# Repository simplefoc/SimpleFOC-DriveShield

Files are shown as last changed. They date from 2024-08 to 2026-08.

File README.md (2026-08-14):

# *Simple**FOC*** ***Drive**Shield* *v1.8*

 
 

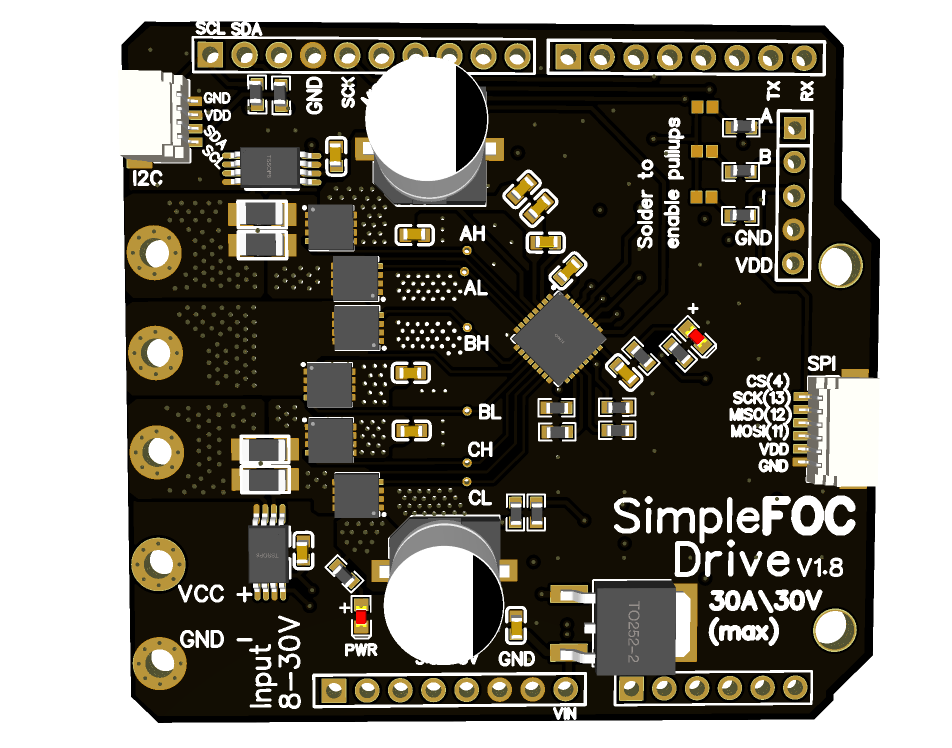
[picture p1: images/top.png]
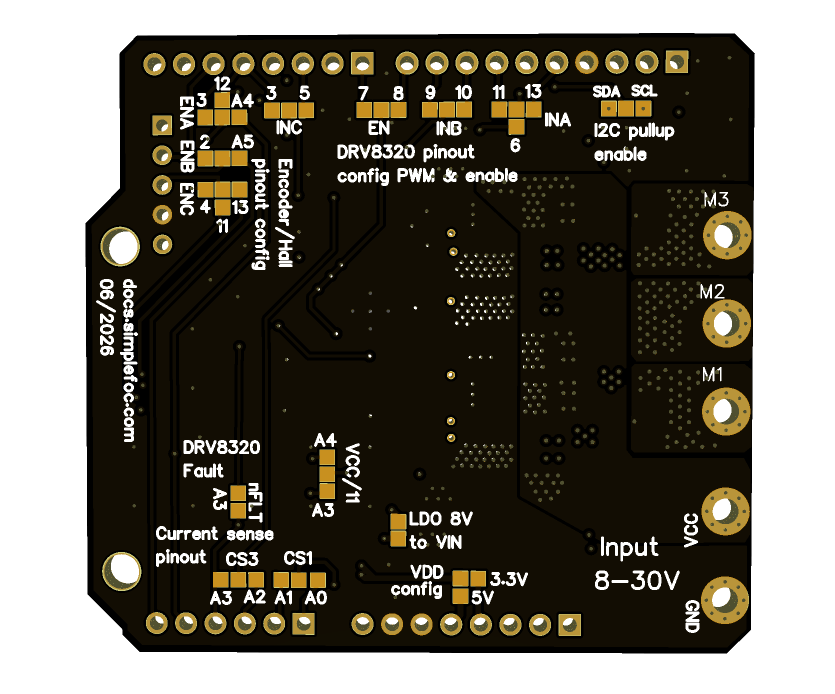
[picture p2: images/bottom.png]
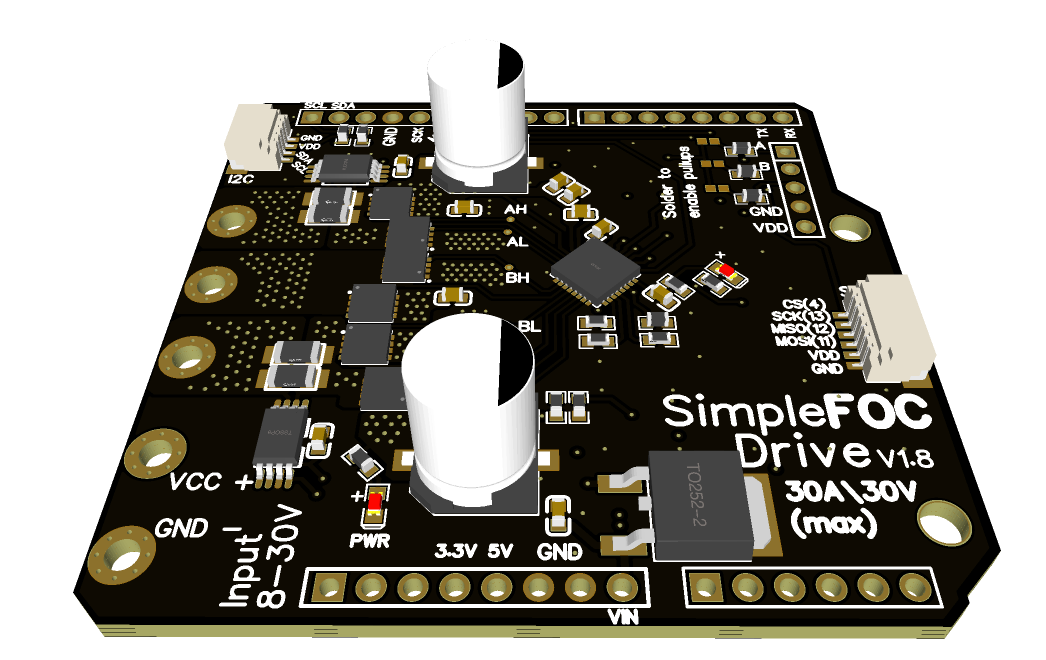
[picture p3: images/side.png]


This is an open-source low-cost BLDC driver boards in the form of a Arduino shield. It is a part of the *Simple**FOC*** project. The board is the big brother of the *Simple**FOC**Shield* and is designed to drive motors with higher current requirements, up to 40Amps. The board is created with the same philosophy as the *Simple**FOC**Shield* - to be simple to use, low-cost, and open-source and fully compatible with the *Simple**FOC***library. 

Additionally the aim of the board is to serve as a template project for the community to build their own motor drivers. 
- The board is relatively simple and can be easily modified to fit different requirements.
- The board is designed in EasyEDA and all the fabrication files are available for download

### Components
- **DRV8320H** gate driver - [datahseet](https://www.ti.com/lit/ds/symlink/drv8320.pdf?ts=178671431434)
   - Hardware configuration 
   - 3PWM 
   - Protections: undervoltage lockout, charge pump fault, MOSFET overcurrent, MOSFET short circuit, gate driver fault and overtemperature
- **BSZ0904NSI** mosfets
   - Standard 3mm x 3mm footprint (can be easily exchanged)
   - Max current 75A 
   - Max voltage 30V
- **INA240A1**: - [datasheet](https://www.ti.com/lit/ds/symlink/ina240.pdf?ts=1786684614540)
   - Inline current sensor
   - Gain 20V/V
   - Shunt resistor: 2mΩ (parallel of 4mΩ)
   - 40A measurement range bidirectional (at 3.3V)
- **LM7808**:
   - 8V LDO voltage regulator to VIN 

### Features
- **Boards absolute max ratings** 
   - Max current: 20A continuous (peak 30A - measured) 
   - Max input voltage: 30V
- **Stackable**: running 2 motors in the same time
- **Encoder/Hall sensors interface**: Integrated 3.3kΩ pullups (configurable)
- **I2C interface**: Integrated 4.7kΩ pullups (configurable)
- **Configurable pinout**: Hardware configuration - soldering connections
- **stemma QT connector**: for easy connection of sensors and peripherals
- **JST SPI connector**: for easy connection of SPI devices (only one SPI device can be connected at a time)
- **Arduino headers**: Arduino UNO, Arduino MEGA, STM32 Nucleo boards...
- **Open Source**: 
   - Fully designed in **EasyEDA**: [EasyEDA project](https://oshwlab.com/the.skuric/SimpleFOC-Drive)
   - Fully available fabrication files - [how to make it yourself](https://docs.simplefoc.com/arduino_simplefoc_shield_fabrication)
- **Low-cost**: Estimated price of 25-40€ - *Will be available through **Makerfabs** soon*

## Shield version comparison

Feature | <span class="simple">Simple<span class="foc">FOC</span>Shield</span> v1.x | <span class="simple">Simple<span class="foc">FOC</span>Shield</span> v2.x | <span class="simple">Simple<span class="foc">FOC</span>Shield</span> v3.x | <span class="simple">Simple<span class="foc">FOC</span> <b>Drive</b>Shield</span> v1.x
|-|-|-|-|-|
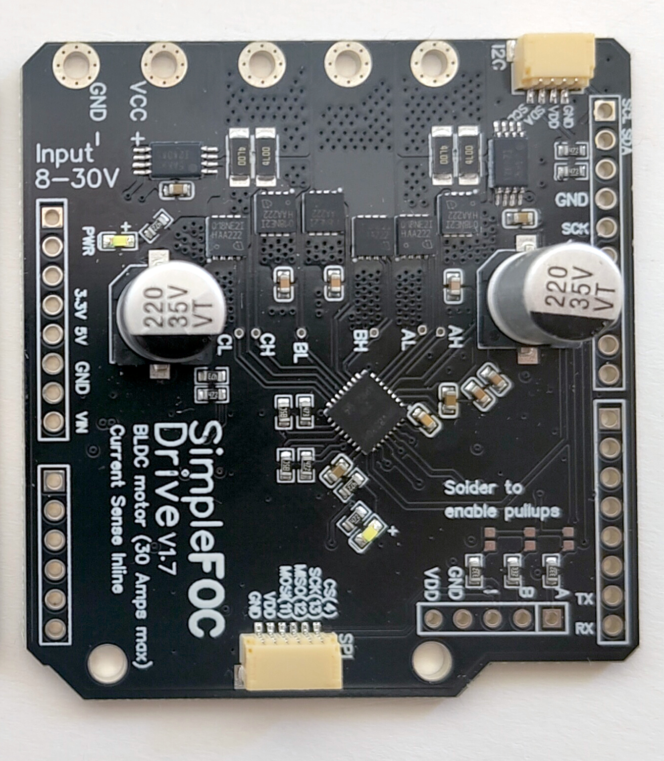
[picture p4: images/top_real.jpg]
|||||
**PWM Driver** | [L6234](https://www.st.com/resource/en/datasheet/l6234.pdf) | [L6234](https://www.st.com/resource/en/datasheet/l6234.pdf) | [DRV8313](https://www.ti.com/lit/ds/symlink/drv8313.pdf?ts=1719165774986&ref_url=https%253A%252F%252Fwww.google.com%252F)| gate driver: [DRV8320H](https://www.ti.com/lit/ds/symlink/drv8320.pdf) <br> mosfets: [BSZ0904NSI](https://www.infineon.com/dgdl/Infineon-BSZ0904NSI-DataSheet-v02_04-EN.pdf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)
**Current Sense** | ❌ | [INA240](https://www.ti.com/lit/ds/symlink/ina240.pdf?ts=1719180172738) | [ACS712 (5A)](https://www.allegromicro.com/en/products/sense/current-sensor-ics/zero-to-fifty-amp-integrated-conductor-sensor-ics/acs712) | [INA240](https://www.ti.com/lit/ds/symlink/ina240.pdf?ts=1719180172738)
**Current measurement range** | ❌ | (configurable) ±3.3/5Amps | ±5Amps | ±40Amps
**Onboard LDO** | ❌ | LM7808 | LM7808 | LM7808 (v1.8+)
**Stackable** | ✔️ | ✔️ | ✔️ | ✔️
**Max current** | 2Amps (5Amp peak) | 2Amps (5Amp peak) | 2Amps (3Amp peak) | 20Amps (40Amp peak)
**Max voltage** | 24V | 35V | 35V | 30V 
**Protections** | Overtemperature | Overtemperature | Overtemperature, Overcurrent | undervoltage lockout, charge pump fault, MOSFET overcurrent, MOSFET short circuit, gate driver fault, overtemperature
**Footprint** | 68mm x 53 mm | 68mm x 53 mm | 56mm x 53mm | 56mm x 53mm
**Design tool** | Altium Designer 2019 | Altium Designer 2019 | EasyEDA | EasyEDA 

## Board evolution timeline

To check the release timeline, click [here](https://github.com/simplefoc/SimpleFOC-driveShield/releases) 

Version  | release | Release date | Comment
----- | ----- | ---- | ----
*Simple**FOC** **Drive**Shield* v1.0 | v0.1 | 05/24 | - Test version <br> - **DRV8300** gate driver <br> - **SE3082G** dual mosfets <br> - ACS712 (range +-30Amps) <br> - 20V max voltage 
*Simple**FOC** **Drive**Shield* v1.0 | v1.0 | 06/24 | - Transition to **DRV8320H** gate driver <br>  - 30V max voltage
*Simple**FOC** **Drive**Shield* v1.1 | v1.1 | 07/24 | - Transition to 3x3mm **BSZ09x** mosfets instead of **SE3082G** <br> - 30V max voltage
*Simple**FOC** **Drive**Shield* v1.2 | [v1.2](https://github.com/simplefoc/SimpleFOC-DriveShield/releases/tag/v1.2) | 08/24 | Initial release <br>- Transition to **4 layer** PCB <br> - Enabling stacking (soldering pads) <br> - Configurable pullups (I2C and encoder) 
*Simple**FOC** **Drive**Shield* v1.7 | v1.7 | 02/26 | - stemma QT connector<br>-SPI connector<br>- INA240 current sensing <br>- Power supply measurement
*Simple**FOC** **Drive**Shield* v1.8 | v1.8 | 06/26 | - added LDO to power the board from VIN (8V) 

## Size comparison with SimpleFOCShield v3

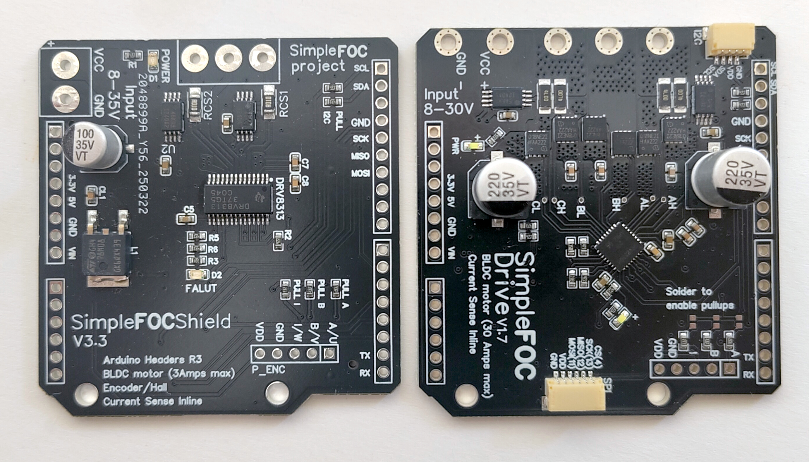
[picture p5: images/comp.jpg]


## Temperature characteristics study

This board can measure the phase currents up to 30Amps, so it is intended to be used in applications that require current draw up to around 20Amps continuous. For higher currents especially in the range of 15-30Amps the board can get quite hot. Depending on the copper thickness of the PCB chosen when ordering the board the temperature can vary, as well as the cooling conditions. The board can be fitted with a heatsink to improve the thermal performance.

So I've wanted to quantify the temperature characteristics of the board when a continuous current is applied to the motor. The measurements were done with a relatively constant ambient temperature of around 25°C. The board was powered with 24V. The motor was run at very low speed (0.1rad/s) in the open loop and the current (q component) was set to 10, 15 and 20 amps for prolonged periods of time. I've measured the temperature on the top of the board on the DRV8320H gate driver and the BSZ0904NSI mosfets. I've used the PICOLOG TC-08 thermocouple data logger to do the measuring.

Two copper thicknesses were tested
1. Standard 4-layer: 
    - **1oz** (35um) copper thickness on top and bottom layers, 
    - **0.5oz** (17.5um) copper thickness on inner layers

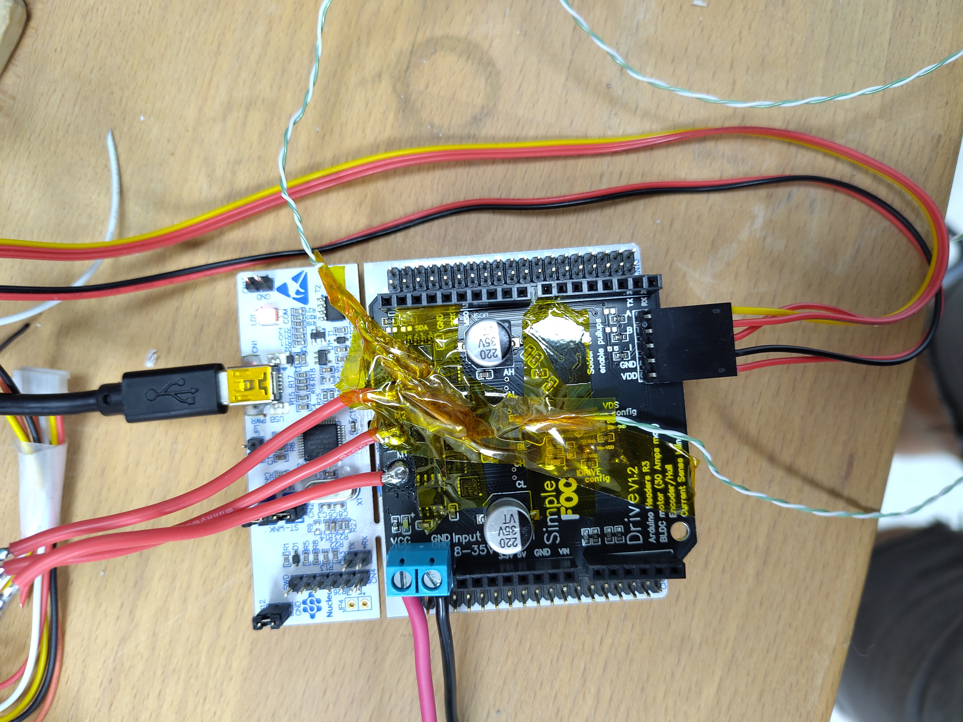
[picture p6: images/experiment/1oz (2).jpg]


2. Thick 4-layer: 
    - **2oz** (70um) copper thickness on top and bottom layers, 
    - **0.5oz** (35um) copper thickness on inner layers

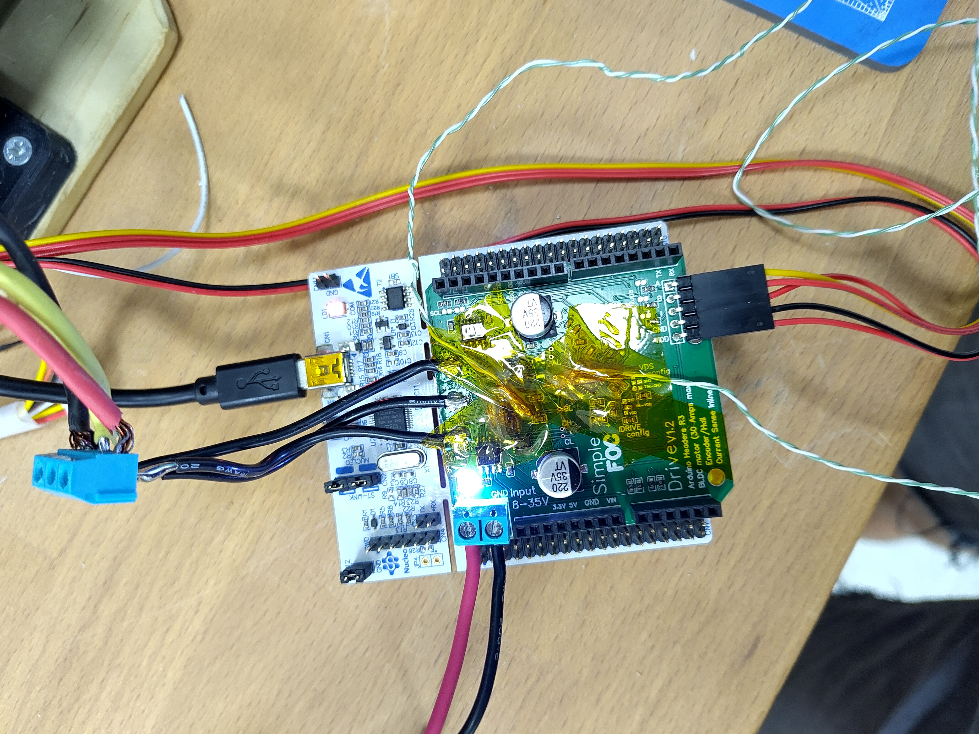
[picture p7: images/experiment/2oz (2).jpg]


### Experiment results
Here is the table of the results

Current [A] | Standard 4-layer MOSFETS | Thick 4-layer  MOSFETS | Standard 4-layer DRV8320 |  Thick 4-layer DRV8320 
--- | --- | ---| --- | ---
10 | 57°C| 53°C | 50°C  | 52°C
15 | 78°C | 68°C| 62°C  | 62°C
20 | 125°C  | 100°C | 82°C | 82°C

So the results seem to suggest that, as the **BSZ0904NSI** mosfets are rated for temperatures up to 150°C and the **DRV8320H** gate driver up to 125°C, the board can be used up to 20Amps without additional cooling. 

**However, I would definitely recommend using a heatsink or a thicker copper PCB (2oz top and bottom layers) for currents above 15Amps continuous.**

<details>
<summary>Measured temperatures during the experiment</summary>

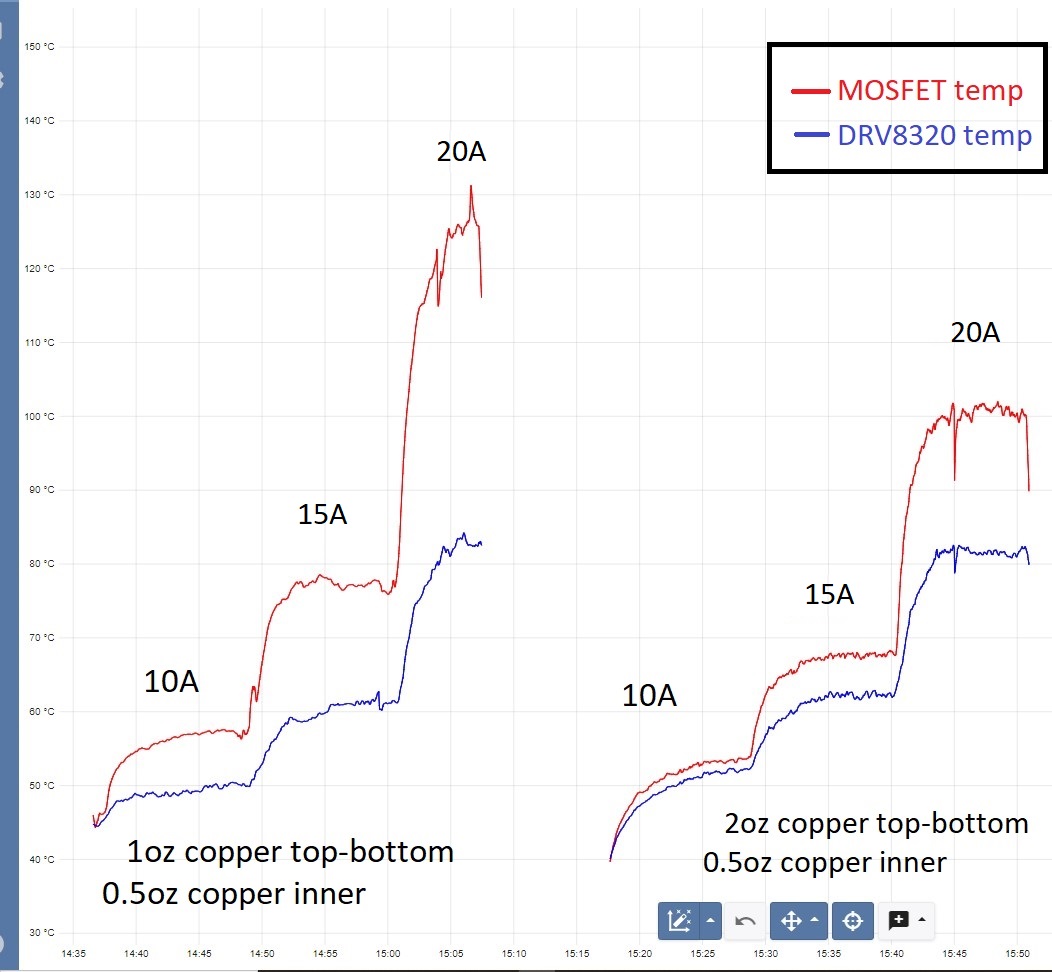
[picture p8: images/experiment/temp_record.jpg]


</details>

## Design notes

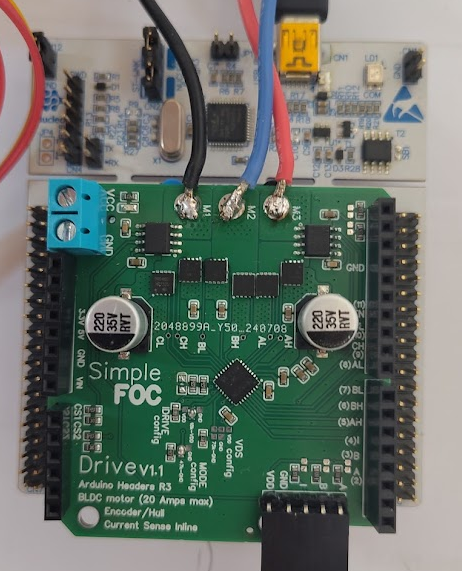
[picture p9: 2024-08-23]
images/nucleo.png

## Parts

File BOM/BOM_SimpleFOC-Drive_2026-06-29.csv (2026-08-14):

ID | Name | Designator | Footprint | Quantity | Manufacturer Part | Manufacturer | Supplier | Supplier Part
1 | C0603B104K160NT | C1,C5,CB1,CB2,CB3, CL1 | C0603 | 6 | C0603B104K160NT | TORCH(火炬) | LCSC | C17702750
2 | 1uF | C4,C6,CBYP3,CBYP4 | C0603 | 4 | CL10A105KB8NNNC | UNI-ROYAL(Uniroyal Elec) |  | C22978
3 | 47nF | C7 | C0603 | 1 | CL10B473KB8NNNC | Samsung Electro-Mechanics |  | C1622
4 | 220uF | C9,C10 | CAP-SMD_BD8.0-L8.3-W8.3-LS9.5-FD | 2 | VT1V221M-CRF10 | VT(首科) | LCSC | C305376
5 | SM06B-SRSS-TB(LF)(SN) | CN1 | CONN-SMD_SM06B-SRSS-TB-LF-SN | 1 | SM06B-SRSS-TB(LF)(SN) | JST | LCSC | C160405
6 | SM04B-SRSS-TB(LF)(SN)(P) | CN2 | CONN-SMD_4P-P1.00_SM04B-SRSS-TB-LF-SN | 1 | SM04B-SRSS-TB(LF)(SN) | JST | LCSC | C160404
7 | LED-0603 | D1,D2 | LED0603 | 2 | KT-0603W | Hubei KENTO Elec | LCSC | C2290
9 | 3.3k | PULL_B1, PULL_A1,PULL_I1 | R0603 | 3 | 0603WAF3301T5E |  | LCSC | C22978
8 | 75k | R8,R9 | R0603 | 2 | 0603WAF7502T5E | UNI-ROYAL(Uniroyal Elec) | LCSC | C23242
9 | 4.7kΩ | R6,R7,R11,PULL_SCL1,PULL_SDA1,R1,R_DV2 | R0603 | 7 | 0603WAF4701T5E | UniOhm | LCSC | C23162
10 | RESISTOR-SMD-1206 | RCS1,RCS2,RCS3,RCS4 | RESISTOR-SMD-1206 | 4 | PMR18EZPFV4L00 | ROHM Semicon | LCSC | C510287
11 | 47k | R_DV1,R10 | R0603 | 2 | 0603WAJ0473T5E | UniOhm | LCSC | C23162
12 | DRV8320HRTVR | U2 | WQFN-32_L5.0-W5.0-P0.50-TL-EP | 1 | DRV8320HRTVR | TI(德州仪器) | LCSC | C701782
13 | BSZ0901NSATMA1 | U8,U9,UB1,UB2,UC1,UC2 | DFN-8_L3.3-W3.3-P0.65-BL-2 | 6 | BSZ0904NSI | Infineon(英飞凌) | LCSC | C534689
14 | INA240A1PWR | U1,U5 | TSSOP-8_L4.4-W3.0-P0.65-LS6.4-BL | 2 | INA240A1PWR | TI(德州仪器) | LCSC | C93965
15 | L78M08CDT-TR | L1 | TO-252-2_L6.6-W6.1-P4.57-LS9.9-TL-CW | 1 | L78M08CDT | ST | LCSC | C158076

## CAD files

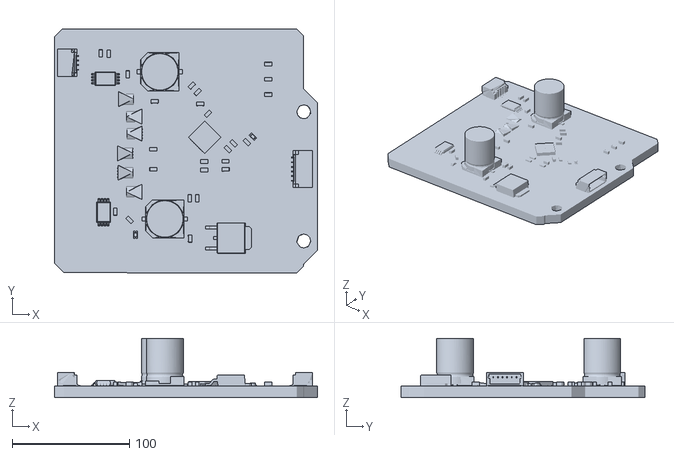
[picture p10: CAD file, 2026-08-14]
3D model/OBJ_pcb_drive.obj
224.3 x 208.5 x 50.4

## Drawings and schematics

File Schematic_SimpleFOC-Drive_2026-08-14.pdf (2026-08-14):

# INA240 Current Sense Circuit

# DRV8320H Gate driver circuit

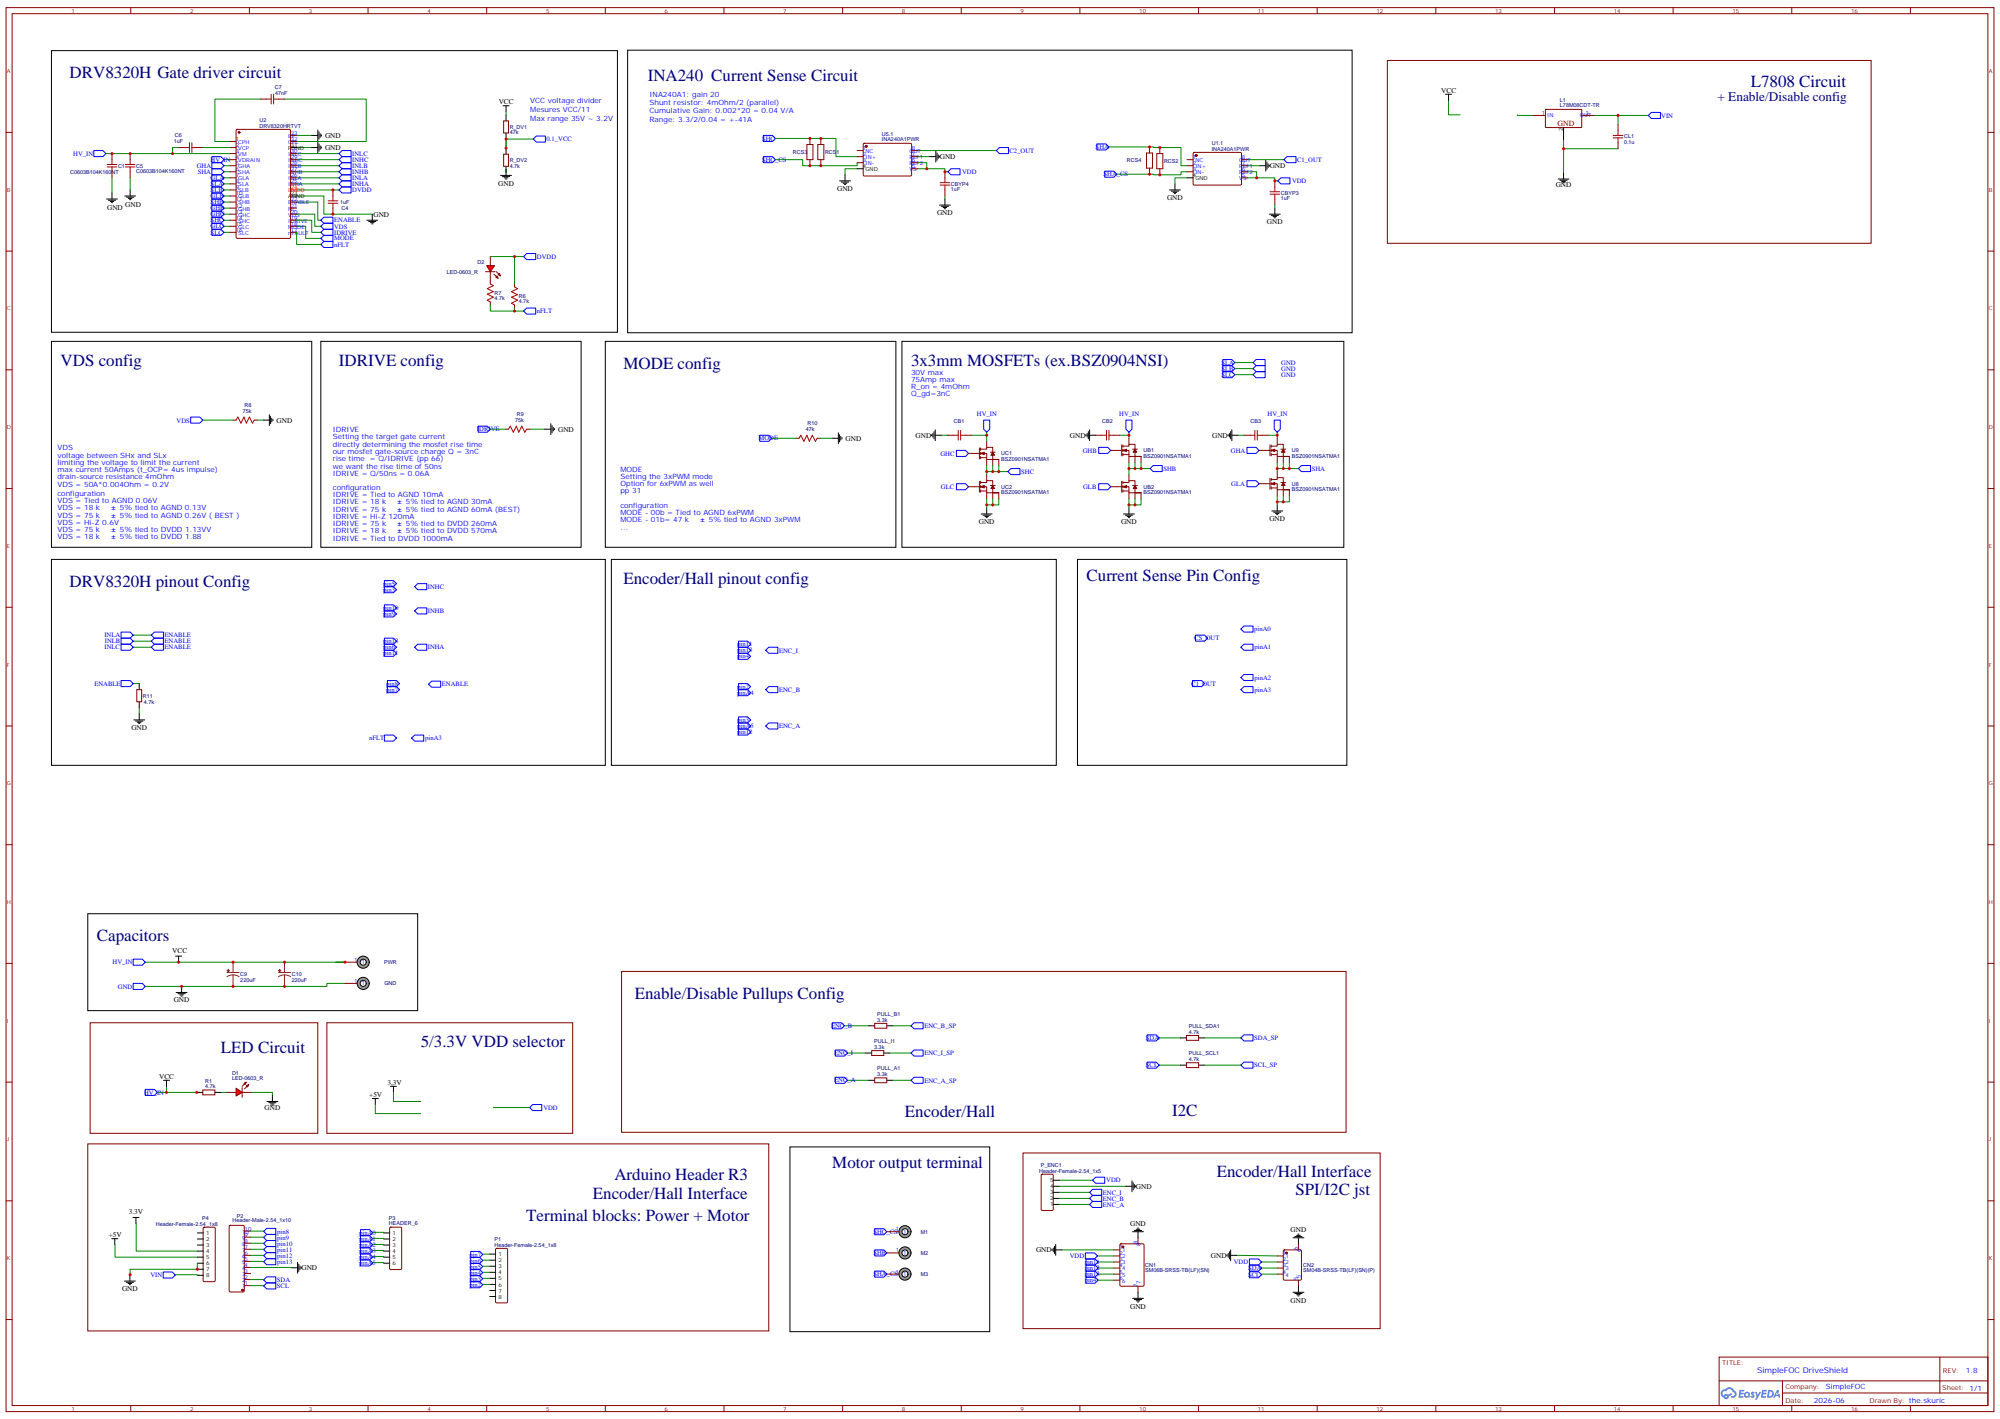
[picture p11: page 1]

Setting the target gate current
directly determining the mosfet rise time
our mosfet gate-source charge Q = 3nC
rise time = Q/IDRIVE (pp 66)
we want the rise time of 50ns
IDRIVE = Q/50ns = 0.06A
configuration
IDRIVE = Tied to AGND 10mA
IDRIVE = Hi-Z 120mA
IDRIVE = Tied to DVDD 1000mA

VDS
voltage between SHx and SLx
limiting the voltage to limit the current
max current 50Amps (t_OCP= 4us impulse)
drain-source resistance 4mOhm
VDS = 50A*0.004Ohm = 0.2V
VDS = Tied to AGND 0.06V
VDS = Hi-Z 0.6V

MODE
Setting the 3xPWM mode
Option for 6xPWM as well
MODE - 00b = Tied to AGND 6xPWM

Current Sense Pin Config

Enable/Disable Pullups Config

Terminal blocks: Power + Motor

SM06B-SRSS-TB(LF)(SN)

Drawn By: the.skuric

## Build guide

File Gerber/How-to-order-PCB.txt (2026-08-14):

How to Order PCB

Please refer to:
https://docs.easyeda.com/en/PCB/Order-PCB

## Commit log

2024-08-23 inital upload
    [BOM_SimpleFOC-Drive_2024-08-23.csv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]
2024-08-23 more details about the temperatures

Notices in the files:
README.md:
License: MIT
